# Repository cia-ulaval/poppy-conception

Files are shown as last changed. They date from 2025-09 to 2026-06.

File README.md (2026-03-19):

# Poppy Humanoid (Conception) 🛠️

## Documentation (_How to Poppy_)
- Visiter ce [Google Docs](https://docs.google.com/document/d/1xX1RbV6WdlQWjZE55EWiICiZSR_HosOSyKKz-T2dgOk/edit?usp=sharing).
- Tu trouveras dans ce document les points marquants de la conception du robot, ainsi que de toutes les manoeuvres et manipulations nécessaires à son bon fonctionnement.

## Fiche d'Identité

*   **Type de projet :** Projet Club
*   **Team Lead :** Cyrille Bernier
*   **Partenaire Académique/Industriel :** N/A
*   **Effectif recherché :** 4 membres
*   **Profils recherchés :** Génie mécanique, Impression 3D, Robotique, Électronique

## Description du Projet

Imprimer en 3D et assembler un robot humanoïde Poppy open-source, comprenant l'impression des composants, l'assemblage des 25 articulations motorisées et l'intégration des systèmes électroniques pour créer un robot fonctionnel.

## Objectifs & Livrables

*   **Objectif Principal :** Construire un robot humanoïde Poppy entièrement fonctionnel pour la session d'automne.
*   **Livrables attendus :**
    *   Pièces imprimées en 3D et post-traitées
    *   Structure mécanique assemblée avec 25 articulations
    *   Système électronique intégré et câblé
    *   Documentation complète du processus d'assemblage
    *   Robot fonctionnel prêt pour la programmation

## Timeline Prévisionnelle de la Session

| Semaine | Activité/Phase |
| :-----: | :--- |
|  **1-2**  | **Planification** - Étude des plans |
|  **3-6**  | **Impression 3D** - Production intensive des composants mécaniques |
|  **7-8**  | **Post-traitement** - Finition et préparation des pièces imprimées |
|  **9-12** | **Assemblage mécanique** - Montage des articulations et structure |
|  **13-15**| **Intégration électronique** - Câblage moteurs et capteurs |

## Technologies & Compétences Visées

*   **Logiciels :** Logiciels CAO (SolidWorks/Fusion360), Slicers impression 3D
*   **Matériels :** Imprimantes 3D, moteurs Dynamixel, composants électroniques
*   **Compétences :** Impression 3D, assemblage mécanique, lecture plans techniques, soudure, câblage

## Pourquoi rejoindre ce projet ?

Tu vas aimer ce projet si :
*   Tu aimes travailler de tes mains et voir un projet concret prendre forme
*   Tu es passionné par la robotique et la mécanique
*   Tu veux apprendre les techniques d'impression 3D et d'assemblage robotique professionnel

## Contact & Liens Utiles
*   **Documentation :** [Poppy Project Documentation](https://docs.poppy-project.org/en/assembly-guides/poppy-humanoid/)
*   **Référence :** [GitHub Poppy](https://github.com/poppy-project)
*   **Fichiers imprimables des Body Parts de Poppy:** [Fichiers imprimables](https://github.com/poppy-project/poppy-humanoid/releases/download/hardware_1.0.1/STL_3D_printed_parts.zip)
*   **Excel des pièces:** [Excel](https://ulavaldti-my.sharepoint.com/:x:/r/personal/cyber18_ulaval_ca/Documents/Poppy%20pi%C3%A8ces.xlsx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)
*   **Playlist vidéos d'assemblage:** [Playlist](https://www.youtube.com/watch?v=SUlM_mE3plc&list=PL8wg9_Kkof8wwqgfFu0iCij73C-4gt95x&index=2)
*   **[Body parts en format .sldprt](https://github.com/poppy-project/Poppy-multiarticulated-torso/tree/dffc1e8f4aaba17622789be21f6563d275080ec6/parts)**

- **[Documentation des moteurs qui n'avaient pas d'allure](https://ulavaldti-my.sharepoint.com/:x:/g/personal/cyber18_ulaval_ca/IQDmeS0tiUcpSrYruJAAcc10AX4TU4iCfaX-LsLGC0McrcA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)**
- [Documentation Poppy Eve](https://github.com/poppy-project/Poppy-eva-head-design#poppy-eve-head-design)

# Démarrage du projet

---

## Prérequis

- Dockers : <https://docs.docker.com/desktop/#next-steps>

---

## Démarrage rapide

```bash
docker compose up -d
```

une fois démaré le conteneur est relié en temps réel au dossier src du projet.

---

## Commandes utiles

```bash
# Démarrer
docker compose up -d

# Arrêter
docker compose down

# Attacher au conteneur
sudo docker attach poppy-dev

#détacher du conteneur (ne pas executer dans ton terminal)
exit

# Voir les logs
docker compose logs -f

# Reconstruire après modification de Package.json ou Dockerfile
docker compose up -d --build

# pour avoir de l'aide à propos des commandes dockers
docker --help
docker compose --help

```

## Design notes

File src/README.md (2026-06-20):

# How to Run Project

```txt
IPv4 adress de Poppy : 10.242.180.129
Procédure pour les noobs : 
ssh poppy@10.242.180.129
password : poppyulaval
cd work/poppy-conception
docker compose up -d
docker attach poppy-dev
exit (pour quitter le terminal)
DISPLAY=:0 python3 src/ui/screen.py depuis work/poppy-conception

```

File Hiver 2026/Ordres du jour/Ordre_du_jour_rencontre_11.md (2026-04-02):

## À faire

- Finir l'*exposure* des données des moteurs.
- Connaître les limites de chaque moteur pour normaliser les sorties et dé-normaliser les entrées
- Finir l'Assemblage du nouveau Chest.
- Ajouter les batteries.
- Tester le nouveau circuit (sans tuer Poppy)
- Cable management (apporter des zip ties)
- Prise Jack DC ?

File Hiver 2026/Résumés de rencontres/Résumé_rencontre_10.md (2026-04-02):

# Fait

Specs Batteries et al.
Rencontre avec Jonathan (Simulation Poppy)

## Cad
- Vis : chambrage circulaire pour accueillir la tête de la vis.
- Imprimé le sac a dos.

## Brand	DROK
- Colour	Aluminium Shell
- Item weight	0.11 Kilograms
- Input voltage	24 Volts
- Output voltage	12 Volts

Dimensions : 
- 5.7x3.8x2.2 cm
- 109 g

## Batterie 3Ah 12V
- Dimensions: 4.33 in. x 1.10 in. x 2.95 in. (110 mm x 27 mm x 75 mm)
- Weight: 0.8 lbs. (0.4 kg)

## Software
- API set-uppé.
- Images de Poppy affichées dans le terminal par Tkinter. (Laurik)
- Bonhomme sourire de Poppy.

# À faire
- Imprimer le nouveau chest
- set-upper le full screen sur l'écran de Poppy. 
- Pendaison de Poppy.
- Être capable de GET la position et vélocité des moteurs. Être capable de lancer une commande sur chacun des moteurs.

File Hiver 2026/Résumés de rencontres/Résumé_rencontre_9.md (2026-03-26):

# API
## Fait
- Exploration
- Set-uppé le SSH.
- AUTRE dont je ne me souviens plus.

Batteries : 
- 8 x 3.8 x 4.5 cm
- Fils sortent par en arriere
- PLaque fixée à l'air libre, sur l'extérieur, protégée et isolée par 7 mm de plastique. 
- On ajoutera une couche d'isolant thermique pour le régulateur.
- Vérifier si l'air est un meilleur isolant thermique que le PLA.
    - Air : 0.024 W/mK
- Vérifier la température maximale ambiante pour les batteries.
- Vérifier le wattage thermique (puissance thermique) du régulateur
- Vérifier l'Aire du régulateur : 

### À acheter : 
- Isolant
- Régulateur
- 

Contraintes (cahier des charges) : 
- La distance entre le support transversal et l'intérieur de l'arrière dos du sac a dos > 4.5 cm.
- La distance entre la base de la poignée et le côté intérieur latéral du sac a dos > 3.8 cm.
- Il doit y avoir de l'espace pour faire passer tous les fils derrière la poignée.
- Il doit y avoir un moyen de fixer le SAD (sac a dos) sur le frame de Poppy.
- Il doit y avoir un moyen de fixer le régulateur sur le SAD.
- Il ne faut pas que la chaleur du régulateur fasse fondre le plastique
- Il faut que les batteries soient logées de façon à ne pas bouger pendant les mouvements.

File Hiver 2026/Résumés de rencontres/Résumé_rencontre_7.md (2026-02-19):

- Vérification de max 5 volts pour le condensateur du RPi.
- La prise mâle qui doit entrer dans le SMPS est une prise de type "Jack DC male"
- Il faudra ajouter un module après la batterie. Pour s'assurer que la tension ne descende pas trop.
- [Convertisseur USB-c à Jack DC 5.5mm a 2.1 mm](https://www.amazon.ca/Female-Input-Charge-Laptop-Notebook/dp/B0BPB8BPRP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) Utile si on a une batterie dont l'extrant aboutit sur un USB-c mâle.
- [USB à Jack DC 5.5 mm x 2.1 mm](https://www.amazon.ca/AAOTOKK-Converter-5-5%C3%972-1mm-Connector-Charging/dp/B0B1WY584Y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) 
    - Utile si on a une batterie dont l'extrant aboutit sur un USB mâle. (not so likely...)
- Batterie qui fournit entre 8 et 12 Ah (8000 mmAh, 12000 mmAh) (valeur d'énergie).
- Batterie va shooter 12V fixes. Mais la batterie peut shooter la quantité de Watts qu'on lui demande, dans les plages de valeurs fixées par notre utilisation.
- Li-on ou Lipo-pack-3s ou Life-Po4-4s
    - Li-on : [bon spécimen de 306g](https://www.amazon.ca/Rechargeable-Powerful-Portable-Suitable-Equipment/dp/B0C2Q6DXRL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)
        - Problème : les dimensions et le poids affichés dans l'image sont pour du 6000 mAh... malheureusement.
    - LiPo-pack-3s
- Il nous faut un BMS. Le BMS est le module de protection dont on parlait.
- On pourrait (il serait même souhaitable) brancher deux (2) batteries en série. De cette façon, on pourra sélectionner des batteries ayant moins d'énergie stockée, et donc un volume moindre. Nous placerions deux batteries, une sur chaque flanc de Poppy.

- [Meilleur spécimen qu'on a](https://ca.lightmalls.com/12v-4000mah-18650-lithium-ion-dc-12-6v-super-rechargeable-battery-pack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). 
    - Specs : 4000 mAh, 12V, 7x5x2 cm. Calcul : 38.4 minutes à elle seule à 60W. Donc pour deux batteries comme ça, ça fait 76.8 minutes !

| Type Batterie | Avantage | Désavantages |
| --- | --- | --- |
| Li-on | Le module BMS est intégré. | Charge simple.  |
| Li-Po | Plus efficace, plus compacte, plus puissante | Risques dans le chargement. Peut exploser. Pas de BMS. |

# À faire : 
- Contacter l'Université pour demander si on peut avoir des batteries [comme ceci](https://www.amazon.ca/Rechargeable-Powerful-Portable-Suitable-Equipment/dp/B0C2Q6DXRL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) dans le local PLT-3778.

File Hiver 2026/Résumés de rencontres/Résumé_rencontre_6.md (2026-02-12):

# Fait
- Gérer le *cable management*
- Gainer les fils d'alimentation au RPi
- Utiliser le kit de soudure efficacement.
- Placer les adhérents sur les pieds.
- Fixer la caméra.
- Fixer le dessus de la tête avec les aimants.
- On a brainstorm pour les batteries.
- Note : les pieds adhérents sont un peu un risque au démarrage. Positif pour la marche, douteux pour le *stand_position*

# À faire : 
- Zach : visiter le GAUL pour mieux comprendre les batteries, voir les options.

# Batteries
- On s'est renseignés
- On a besoin de ...
    - 12 V
    - 5 A
    - 60 W
- On essaye que ce soit pas moins au niveau des Watts.
- On essaye que ce soit pas moins ni plus au niveau des Volts.
- Combien de kilowattheures avons-nous besoin ?
- Objectif : on veut 15 mintues
- Contrainte : peut-on recharger les batteries toutes du même coup avec le même fil?
    - Zach : peut-être, si on a un bloc pour toutes les charger d'un coup.
- [Possibilité de batterie. Lien.](https://www.alibaba.com/product-detail/10000mah-Type-C-PD-60W-Power_60637098016.html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)

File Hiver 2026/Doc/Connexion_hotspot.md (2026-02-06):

# Comment lancer des primitives à Poppy à partir de la connexion au Hotspot (pour Windows):

- Installer [Postman](https://www.postman.com/). Le télécharger sur sa propre machine (laptop)
- Ne pas se connecter à Postman avec un compte. Si nécessaire, se connecter puis se déconnecter.
- Lancer le robot (alimentation *on*)
- Se connecter à partir de sa machine sur le hotspot de poppy.
    - Mot de passe : poppyproject
- Aller sur un *browser* web. Rentrer l'ip suivant : 
    - 10.99.99.1
- Cliquer sur le bouton *what is happening ?*
- Reboot Robot API
- Revenir au menu principal
- Aller dans Monitor and Control
- On peut alors voir la température en *live* des moteurs.
- Aller sur Postman sans être connecté.
- Toutes les requêtes commencent par l'ip de poppy et son port : 
    - 10.99.99.1:8080/.......suite
- Lancer la requête GET suivante pour obtenir la liste des primitives: 
    - primitives/list.json
- Liste de toutes les requêtes : 

```txt
/robot.json
/ip.json
/motors/list.json
/motors/aliases/list.json
/motors/<alias>/list.json
/motors/<motor_name>/registers/list.json
/motors/<motor_name>/registers/<register_name>/value.json
/motors/registers/<register_name>/list.json
/sensors/list.json<br>/sensors/<sensor_name>/registers/list.json
/sensors/<sensor_name>/registers/<register_name>/value.json
/sensors/camera/frame.png
/sensors/code/<code_name>.json
/records/list.json
/records/<move_name>/value.json
/primitives/list.json
/primitives/running/list.json
/primitives/<primitive_name>/start.json
/primitives/<primitive_name>/stop.json
/primitives/<primitive_name>/pause.json
/primitives/<primitive_name>/resume.json
/primitives/<primitive_name>/properties/list.json
/primitives/<primitive_name>/properties/<prop>/value.json
/primitives/<primitive_name>/methods/list.json
/ik/<chain_name>/value.json
/ik/<chain_name>/rpy.json

Post method url:
/motors/<motor_name>/registers/<register_name>/value.json
/motors/<motor_name>/goto.json
/motors/goto.json
/sensors/<sensor_name>/registers/<register_name>/value.json
/records/<move_name>/record.json
/records/<move_name>/save.json
/records/<move_name>/play.json
/records/<move_name>/stop.json
/records/<move_name>/delete.json
/primitives/<primitive_name>/properties/<prop>/value.json
/primitives/<primitive_name>/methods/<method_name>/args.json
/ik/<chain_name>/goto.json
```

- Par la suite, on peut lancer des requêtes GET pour les primitives de Poppy, dont notamment stand_position, avec la syntaxe suviante : 
    - 10.99.99.1:8080/primitives/stand_position/start.json
- ATTENTION ! Les primitives qui ne sont pas stoppées avec stop.json reviendront éventuellement dans le comportement de Poppy. Autrement dit, elles ne sont pas arrêtées.

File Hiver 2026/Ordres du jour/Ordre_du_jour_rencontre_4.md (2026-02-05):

# à Faire

- Féliciter Toute l'Équipe, mais spécialement Samy.
- Régler les jambes : 
    - Par herborist (reconfiguration des moteurs) ?
    - Par la mécanique ? (Par l'assemblage)
- Souder

- Configure motors correctly

- Peut-être installer les aimants sur la tête.
- Tester d'Autres positions de base.
- Régler la tête qui se positionne mal dans la position standing.
- Commencer les recherches sur les batteries.
- Brainstorm sur l'installation des logos et batteries.
    - Vérifier les amplitudes de mouvement pour toutes les positions de base. De cette façon, nous pourrons mieux cerner les *spots* de Poppy qui sont disponibles pour l'installation d'une extension.

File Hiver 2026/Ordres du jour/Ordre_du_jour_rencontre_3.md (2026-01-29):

# Salut
# À apporter 
- Plus de tie-wraps.

# À faire
- Vectoriser le logo de l'AESGUL.
- Designer la pièce pour le logo de l'AESGUL (SolidWorks).
- Fixer la tête (dernière étape)
- Coller la caméra (parmi les dernières étapes).
- Aller au magasin d'électronique pour : 
    - Souder les fils noirs et rouges ensemble : noir et noir, rouge et rouge.
    - Ça sert à connecter le RPi au Power venant des RS485 extérieurs.
- *Cable management* : 
    - Fixer les câbles avec des boucles 3D-printed.
    - Ou encore des tie-wraps.
    - Ou encore avec de la colle chaude.
    - Ou encore avec de la gommette.

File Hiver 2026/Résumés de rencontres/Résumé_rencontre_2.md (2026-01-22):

# Fait

- Installation de Herborist sur la machine de Samy.
- Fixation de l'écran sur la tête.
- Connexion du POWER entre les deux SMP2S avec des câbles à 3 brins plutôt que des câbles à 4 brins (Samy).
- Vérification que tous les moteurs sont branchés et présents (scan sur Herborist).
    - Configuration du moteur r_ankle_y.
- 
- Le code est installé (Laurik).
- Installation de la caméra (Zach). Branchée provisoirement.
- Élaboration d'un plan d'action pour la connexion de l'adaptateur RPi. (fils rouge et noir).
- 

# À faire
- Fixer la tête (dernière étape)
- Coller la caméra (parmi les dernières étapes).
- Aller au magasin d'électronique pour : 
    - Souder les fils noirs et rouges ensemble : noir et noir, rouge et rouge.
    - Ça sert à connecter le RPi au Power venant des RS485 extérieurs.
- *Cable management* : 
    - Fixer les câbles avec des boucles 3D-printed.
    - Ou encore des tie-wraps.
    - Ou encore avec de la colle chaude.
    - Ou encore avec de la gommette.

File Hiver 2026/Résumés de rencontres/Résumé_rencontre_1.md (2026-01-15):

# À prévoir
- Imprimer des pièces de rechange pour les pièces qui demanderont des réparations.
- Apporter des tie-wraps / zip-ties pour fixer les *dispatchers* de courant. Minces.

# Fait ajd
- Un peu de documentation
- Préparation fichier STL pour le RPi support (*Head Assembly*)
- Cad pièce alternative pour le *HeadLock* Poppy Eva.
- Derrière de la tête 
- Vérification du cablage dans le torse (samy)
- Documentation session passée (Cyrille)
- Tête Arduino (Zach)
- Batteries recherche (Zach (et Cyrille))
    - Besoin de batterie : 3A, 5V.

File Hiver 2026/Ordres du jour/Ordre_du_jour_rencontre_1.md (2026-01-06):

# Retour sur la session d'automne 2025
## Accomplissements
- Robot assemblé
- Cocktail des projets
- Travail d'équipe et ponctualité
- Plaisir

## À changer. 
- Travailler davantage au VCH-3870 lors des journées de développement (Cyrille doit gérer ça mieux).

## À terminer
- Documentation
- Tête : 
- Raspberry Pi : 
    - Trouver le code en ligne : Samy
    - Partager le lien sur le Discord.
    - Intégrer le code sur le Raspberry Pi : toute l'équipe.
    - **Faire marcher le robot pour la première fois.** Deadline : **30 janvier 2026**

# Plan pour la session d'hiver 2026
## À terminer
Voir ci-haut.
## À entreprendre
- Construction du sac à dos de support de batterie.
    - Conversations avec l'équipe de projets pour savoir si on peut avoir le budget pour se payer cette batterie (Cyrille).
    - Identification des besoins électriques de Poppy (Zach et Laurik et Louis)
    - Consultation sur le web de batteries suffisamment fortes pour soutenir Poppy (Samy et Cyrille)
    - Achat de la batterie si le modèle est compatible (taille, prix, autres contraintes, etc.)
    - Modélisation du sac à dos
        - Décider de la pièce sur laquelle attacher le sac à dos.
        - Décider de la méthode de fixation du sac à dos sur le corps de Poppy.
        - Prévoir un moyen de retirer la batterie pour la recharger, ou encore de la recharger directement lorsque fixée sur Poppy.

## Horaire
- CrabFit.

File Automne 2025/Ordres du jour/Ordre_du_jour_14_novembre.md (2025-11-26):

### À faire : 
- Composer le PowerPoint.
- Demander qui sera présent ?
- ~~Demander qui fera le micro-pitch ?~~
- Qu'est-ce que vous aimeriez montrer de notre démarche dans la présentation, dans le pitch, dans le kiosque.
- Définir le plan de présentation : 
    - Points forts, défis, checkpoints, techniques et méthdoes.
    - 5 minutes de présentation.
- Affiche ?

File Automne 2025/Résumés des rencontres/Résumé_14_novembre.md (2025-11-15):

### Présences : 
- Samy
- Cyrille
- Zach
- Laurik
- 

### *Micro-pitch*:
- Zach se propose de le faire.

### Ce que vous aimeriez avoir de présent dans la présentation de 5 mintues : 
- Défis
- Bons coups
- *Checkpoints*
- Méthodes : 
    - Configuration des moteurs
    - Assemblage avec clés allen
    - Sens des pièces (HN07-N101)
    -

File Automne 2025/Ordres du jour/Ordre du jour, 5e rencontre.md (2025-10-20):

- Remplir le CrabFit pour la formation sur SW
- Commencer à assembler.

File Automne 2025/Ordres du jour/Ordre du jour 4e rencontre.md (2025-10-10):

- Merci Zach pour les impressions !
- Finaliser l'installation des logiciels pour la configuration des moteurs.
- Test de configuration des moteurs.
- Assemblage.

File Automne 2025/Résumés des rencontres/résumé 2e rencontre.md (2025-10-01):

# Résumé de la rencontre 26 septembre 2025

## Résumé de la rencontre
- Laurik ferait des recherches sur la calibraiton de l'imprimante en fonction du type de fil, de la marque du fil.
- À faire pour la semaine prochaine : 
    - Visionner les vidéos

## Paramètres à fixer et commandes utiles

### Paramètres
- Sparse and fill / Gyroid (pattern de filling)
- Strength / Wall loops : 4
- Supports / Top Z distance : entre 0.2 et 0.4. En ce moment, laisser à 0.3 max.  Idéal 0.28
- First layer expansion : 3.0
- Qualité / Layer height : 0.18 mm.

- Project filaments / 
    - 3 points / Edit / Textured PEI plate 60 et 60 degrés Celcius
    - Nozzle initial layer : 220 Celcius, other layers : 190 Celcius.
    

- Supports / 
    - threshold angle = 15
    - remove small overhangs = false
    - initial layer expansion = 2
    - top Z distance = 0.28
    - bottom z distance = 0
    - Base pattern = Hollow
    - Top interface layer = 3

### Commandes
- Commande pour visualiser les zones d'opération de la buse par objet : 
    - Aller dans Objects / Plate1 et placer le curseur sur la pièce pour voir son range.

## Outils nécessaires à apporter
- Petits tournevis
- Pinces précises
- Exacto plus coupant
- Papier sablé 80 - 120

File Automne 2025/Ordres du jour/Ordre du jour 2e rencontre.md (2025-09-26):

| # Numéro  | Description | Notes | 
|---|---|---|
| #1  | Clés ? PLT-3905-Z ? | Louis avait quelque chose à dire là-dessus. (insight) |
| #2 | Retour sur la semaine précédente.  |  |
| #3 |  Qualité des faces...  |  |
| #4 |  Calibration de l'imprimante en fonction du type de fil. |  |
| #5  | Paramètres pour ajuster la distance des supports. | Zach ? |
| #6 |  **Warnings** |  |
| #7 |  Début de l'assemblage | Arrimage des Servo-moteurs sur les bras de Poppy. Vis entre les mains et les avant-bras. |
| #8  | |  |
| # | |  |

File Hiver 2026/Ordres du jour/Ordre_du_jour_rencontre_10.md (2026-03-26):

## À faire

- API.
    - Update sur les avancements de l'API.
- Commander l'électronique.
- Cadder le sac à dos.
- Exporter le fichier du sac à dos et celui du torse de façon à pouvoir les imprimer..
- Est-ce que l'API sera prêt pour le 9 avril prochain ?
- 

Hardware
- Pendaison de Poppy.
- Cadder.

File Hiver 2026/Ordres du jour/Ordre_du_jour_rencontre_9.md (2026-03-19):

# À faire

- Set-upper l'API
    - Samy et Laurik, svp dispatcher les tâches si possible.
    - Peut-on commencer les fichiers code de mouvement pour les moteurs ?
        - Code de la puissance et de l'électricité
        - Code du mouvement angulaire des moteurs.

- Sac à dos : première itération. Deuxième itération en cad.
- Feedback sur la première itération : objectif : avoir de quoi sur lequel pointer pour exprimer nos idées.

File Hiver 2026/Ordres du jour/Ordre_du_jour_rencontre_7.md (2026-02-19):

# À faire : 
- Comment ça va ?
- Tempête des sciences : 
    - Mercredi 15 avril, 11h00 - 16h00
    - Présentation de Poppy.
- Être en mesure de push du code à Poppy :
    - Avec fil
    - Sans fil
- Se renseigner sur la façon de faire marcher Poppy : 
    - Code en ligne ?
    - Possible de le télécharger ?
    - Comment le push sur le RPi ?
- Batteries : nouvelles ?
    - Il faut aussi trouver un fil qui transfère le courant depuis la batterie jusqu'à la prise du *dispatcher* de courant
- Composer du code pour le plaisir de voir Poppy dabber (*sidequest* de Cyrille)

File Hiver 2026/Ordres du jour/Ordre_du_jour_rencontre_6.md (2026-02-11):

# À faire

- ALLO !!!

- Ajouter les aimants pour la tête.
- Fermer la tête pour de bon
- Coller la caméra de façon à ce qu'on puisse l'utiliserr
- Remplacer un câble dans la tête (l'allonger) (celui qui est USB)
- *Set-upper* l'écran
- Gérer la *cable management*
- Ajouter l'adhérent aux chaussures.
- Cadder
- Élaoration de primitives
- Ajouter des gaines permanentes

- Brainstorm sur l'autonomisation de Poppy.

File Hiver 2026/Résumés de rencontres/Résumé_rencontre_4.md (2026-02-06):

# Fait

- Travail sur la connexion WiFi de Poppy. Connexion établie entre le HotSpot de Poppy et le laptop de Samy.
- Vérification pour chaque moteur si oui ou non il est à la bonne place.
- Penser au fait qu'il existe 4 erreurs possibles : 
    1. Erreur de nom de moteur : exemple : le actual l_shoulder_y devrait plutôt être r_shoulder_y.
    2. Erreur de fixation entre le moteur et la roulette métallique.
    3. Erreur de fixation entre la roulette métallique et la pièce de plastique.
    4. Erreur dans le positionnement (notamment le sens, l'orientation) de la pièce de plastique par rapport au moteur. 
- Connexion du laptop de Laurik au Poppy Software
- Soudure
- Fixation de la tête vérifiée (démontage et remontage.) On n'était pas sûrs si elle était bien fixée au niveau du *neck*

### Moteurs à reconfigurer (remplacer le nom dans la configuration)
- l_shoulder_y : FAIT
- r_shoulder_y : FAIT
- Pour cela, il fallait démonter le bras, puis le remonter (longues tâches d'environ 2 heures combinées totales)

### Moteurs desquels replacer le membre
- Aucun

# À faire:
- Changer le mot de passe de Poppy.
- Designer le cable management.

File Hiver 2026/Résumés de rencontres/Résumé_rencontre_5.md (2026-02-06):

# Fait

- Ajout de gaines temporaires sur le les soudures d'étain
- Connecté Cyrille et Laurik (leur laptop)
- Confirmation de présence aux portes ouvertes de l'Université Laval le 7 février. (Samy au moins) Voir doc sur la procédure à suivre pour la connexion au Hotspot de Poppy et le lancement de primitives.

# À faire
- Ajouter les aimants pour la tête.
- Coller la caméra de façon à ce qu'on puisse l'utiliserr
- Remplacer un câble dans la tête (l'allonger) (celui qui est USB)
- *Set-upper* l'écran
- Gérer la *cable management*
- Ajouter l'adhérent aux chaussures.
- Cadder
- Élaoration de primitives
- Ajouter des gaines permanentes

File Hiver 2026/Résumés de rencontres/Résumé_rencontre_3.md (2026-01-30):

# Fait

- Gestion du câblage dans la tête.
- Tentatives d'établissement de la connexion entre le RPi et le WiFi.
- But de ces tentatives : commander Poppy à distance. Exemple : "avance le bras"
- Esquisses de vectorisation du logo de l'AESGUL.
- Démarches de *brainstorming* pour l'installation du logo sur Poppy.

# À faire : 
- Souder les fils pour l'alimentation du Rpi
- Achever la connexion réseau de Poppy (Samy et Laurik)
- Mieux déterminer la nature et l'emplacement des batteries sur Poppy (Zach et Cyrille)
- Poursuivre le travail sur le logo de l'AESGUL.
- Modéliser en 3D le support pour le logo (sûrement par essais-erreurs, ou bien en se fiant au modèle .sldprt suivant : [fichier .sldprt](https://github.com/poppy-project/Poppy-multiarticulated-torso/tree/dffc1e8f4aaba17622789be21f6563d275080ec6/parts))
- Modéliser les supports pour les batteries.
- Peut-être : modéliser une pièce qui aurait pour double fonction de soutenir une batterie et d'afficher le logo du partenaire.

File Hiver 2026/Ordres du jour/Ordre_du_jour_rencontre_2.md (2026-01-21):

# À faire
- Mercredi après-midi : cadder mieux les fixations pour la tête (Cyrille).
- Fixer l'écran à la tête (tous).
- Intégrer le code.
- Fermer la tête.
- Documentation en parallèle.
- Définir les batteries à acheter.
- Définir les pièces supplémentaires à acheter.
- Définir un budget pour toutes ces pièces.

# À apporter
- Patafix (Cyrille)
- Tie-Wraps (Cyrille)

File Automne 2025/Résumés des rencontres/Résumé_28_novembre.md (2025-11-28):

# Débriefing du le cocktail des projets (27 novembre)
- À refaire
- Top de recevoir des idées et des commentaires positifs ewt constrcutiis sur notre projet.
- Les gens étaient vraiment intéresés et curieux sur notre projet.
- Les gens ont beaucoup demandé ce que pourrait éventuellement faire Poppy.
- Les juges nous ont défavorisé parce qu'il n'y avait pas d'IA d'implémentée dans notre projet.
- Voir des gens hors du Club était valorisé pour les Team Members.
- **Plus qu'il y a de monde, mieux c'est.**
- **Les Team Members sont très intéressés par la présence accrue de partenaires et d'autres compagnies non partenaires.**
- 

# Brainstorm pour la suite des choses, (Hiver 2026)
- Poppy comme la nouvelle mascotte du Club.
- Idées : 
    - Samy : sac à dos à batterie.
    - Mains articulées.
    - Tout ce qui a trait à l'automatisation.
    - Renforcer la structure en impression 3D
    - Améliorer l'esthétique de la mascotte du Club. Cacher les lieux de fils et de vis nombreux.
- Zach, Samy et Laurik seraient très heureux de poursuivre le projet à la session d'hiver 2026.

# Liste des choses à faire sur Poppy
- (Conception du sac à dos ?)
- Trouver les specs des moteurs
- Mise au point des problèmes avec la tête.
- Intégration logicielle sur Poppy. Ordre des manipulations.
- Adhésion des pieds.
- Impression de pièces de rechange (?, prévision)
- CAD des adhésions pour les pieds.
- Zach va créer un fichier qui documentera les paramètres des impressions pour chacune des pièces.
- Il faut créer un document *How to Poppy*. Ce sera une tâche commune.
    - Mentionner le GitHub et la playlist des assemblages.
    - Configuration des moteurs.

## Pour réussir à faire marcher Poppy
- Tête à imprimer
- Le câblage à connecter
- L'écran / microprocesseur
- Intégrer le code sur le RP pi.
- Tests avec *power supply* et code en ligne.

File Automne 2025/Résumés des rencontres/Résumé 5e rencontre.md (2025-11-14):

- Écrire un guide d'utilisation pour l'imprimante
- Faire une liste de toutes les pièces de Poppy

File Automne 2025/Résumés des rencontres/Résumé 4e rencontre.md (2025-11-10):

# Avancement ?
- **Bras gauche terminé !!!**
- Samy et Cyrille ont installé poppy-configure sur leur Linux.
- Les moteurs MX-64AT sont montés et configurés.
- Les moteurs des hanches sont montés et configurés.
- Les moteurs des épaules et des bras sont tous configurés.

# Procédure installation poppy-configure
- Être sur Linux.
- Installer un environnement python dans un dossier local.
- Activer cet environnement python avec une commande de type "source bin/activate" (dans poppy-env)
- Installer poppy-configure : python3 install poppy-humanoid
- Commande pour configurer : poppy-configure humanoid < motorname >

# Notes : 
- Acheter et apporter du papier sablé (éventuellement)
- Samy ou Cyrille apporte des clés Allen de tailles plus grosses.

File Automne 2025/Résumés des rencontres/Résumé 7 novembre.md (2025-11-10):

### À apporter pour la prochaine rencontre :
- Pince supplémentaire
- Colle chaude

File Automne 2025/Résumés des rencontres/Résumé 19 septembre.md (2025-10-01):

# Résumé rencontre 19 septembre
- Nous nous sommes présentés.
- Nous avons convenu d'un mode de fonctionnement : se relayer pour imprimer les pièces de *Poppy*.
- Nous avons convenu qu'il pourrait être bénéfique de se synchroniser à 2 étudiants pour les impressions de la première semaine.
- Nous avons convenu du jour et de l'heure des rencontres : **les vendredis 16h30, au PLT-3778**
- Nous avons convenu qu'il fallait que chacun ait accès à la clé du local. 
    - Pour ce faire, vous pouvez aller au local **PLT-3905-G** et demander d'avoir une copie de la clé. Ça requiert un dépôt de 20$, qui vous sera rendu à la fin du projet. Le plus tôt que vous avez la clé, le plus tôt que vous pouvez imprimer de votre côté ! Si vous n'avez pas la clé encore, juste faire signe à Amen Ouannes dans le *group chat* (ou la demander à un autre *Team member*)
- Nous avons discuté des procédures d'impression.

# Procédure d'impression:
1. Importer la pièce dans Bambu Studio.
2. Vérifier la couleur de la pièce.
3. Orienter correctement la pièce pour l'impression. Critères : surface plane par-dessus un vide limitée; les cercles doivent avoir leur rayon dans le plan *xy*.
4. Ajouter les supports si nécessaire.
5. Trancher le plateau.
6. Exporter le fichier tranché sur la clé USB (connetée à la carte SD).
7. Éjecter la clé USB.
8. Insérer la carte micro-SD dans l'imprimante.
9. Choisir le fichier à imprimer.
10. Sélectionner la couleur d'impression.
11. Appuyer sur *Imprimer*.

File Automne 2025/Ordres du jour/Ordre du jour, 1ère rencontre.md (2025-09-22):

| # Numéro  | Description | Notes | 
|---|---|---|
| #1  |  **Présentations**, baccalauréats, intérêts personnels, hobby, phobie, folie.  |  |
| #2 | Présentation de l'**échéancier** pour la session.| Mentionner que c'est modifiable. |
| #3 | Présenter l'**imprimante 3D**. | Julie présentation, demande si les gens connaissent bien l'imprimante 3D. Présenter les paramètres importants. |
| #4 | Présenter la visée des quelques **prochaines semaines**  | Impression intensive, distribution des impressions. Beaucoup du travail se fera individuellement. Logistique des **clés** et des **cartes SD.** |
| #5  | Installation du logiciel **BambuStudio** | Installation du logiciel, importation des membres Poppy Humanoid |
| #6 | **Assigner** les différentes impressions à chacun des membres. | |
| #7 | Impression collective de la **première pièce** de *Poppy*. | |
| #8  | Convenir d'une **plage horaire** dans la semaine où nous pouvons nous rencontrer pendant la session. Utilisation de CrabFit. | |
| # | | |

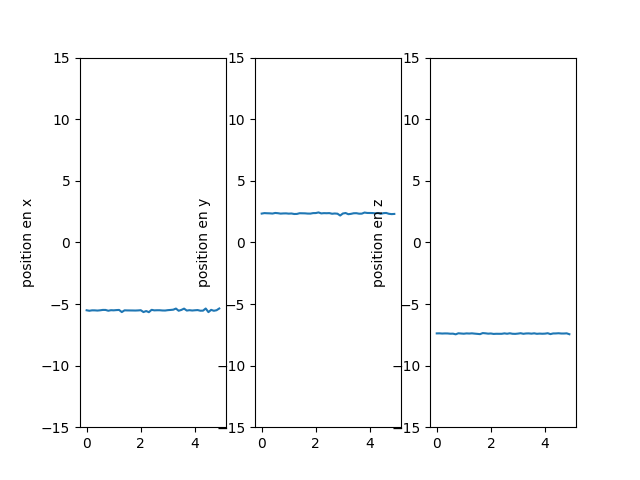
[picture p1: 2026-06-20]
src/accelerometres/avec_le_clone/acceleration.png

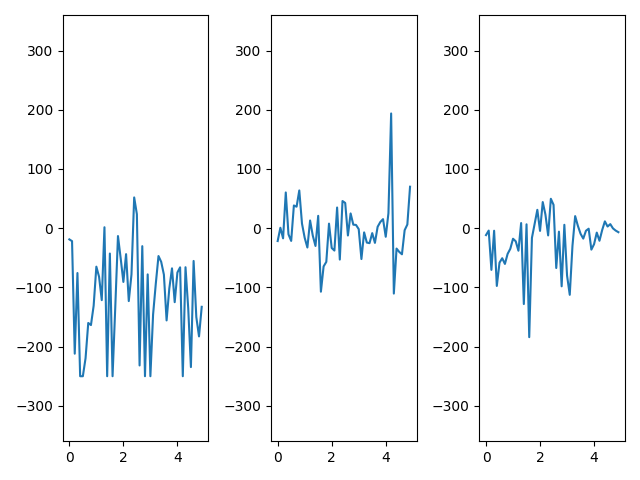
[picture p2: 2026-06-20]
src/accelerometres/avec_le_clone/angles.png

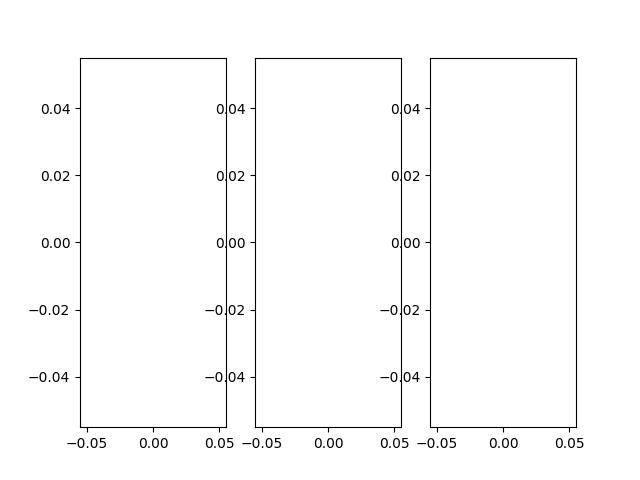
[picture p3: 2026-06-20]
src/accelerometres/avec_le_clone/vitesses_angulaires_live.png

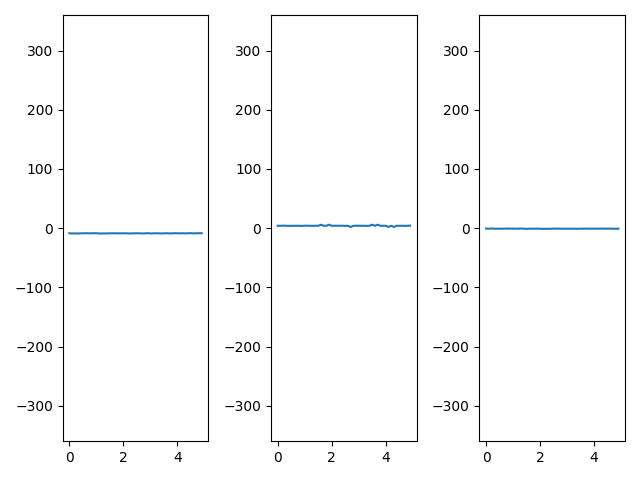
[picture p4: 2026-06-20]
src/accelerometres/avec_le_clone/vitesses_angulaires.png

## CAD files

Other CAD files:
connexion m28 manquante.gcode.3mf

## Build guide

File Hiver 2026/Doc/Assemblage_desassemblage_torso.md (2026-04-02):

Enlever bras
Enlever shoulder connecter
Enelver les moteurs cen traux

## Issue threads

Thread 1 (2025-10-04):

Preprocess the data.

JeromeCGithub, 2025-10-04:
On a pris un set de donnée avec le bracelet qui se trouve sur la branche :

Ce ticket consiste à analyser la donnée, la comprendre puis splitter la data avec scikit en training data et en target data. Voir la doc de scikit : https://scikit-learn.org/stable/modules/generated/sklearn.discriminant_analysis.LinearDiscriminantAnalysis.html

Ensuite, essayer d'entrainer des modèles avec plusieurs algorithmes trouvable ici : https://libemg.github.io/libemg/documentation/prediction/prediction.html

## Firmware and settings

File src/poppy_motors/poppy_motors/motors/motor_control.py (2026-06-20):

from time import perf_counter, time

from dynamixel_sdk import (COMM_SUCCESS, PortHandler,PacketHandler, GroupSyncWrite, GroupBulkRead)
from concurrent.futures import ThreadPoolExecutor


PORTS = ['/dev/ttyACM0','/dev/ttyACM1']
PROTOCOL = 1.0
ID_RANGE = range(0, 55)
BAUDRATE = 1000000





class MotorController:
    """
    Manages communication with multiple motors over serial ports, handling
    port initialization, baud rate configuration, motor ID mapping, and
    resource cleanup.
    """


   


    def __init__(self):
        self.port_handlers : list[PortHandler] = [PortHandler(port) for port in PORTS]
        self.packet_handler : PacketHandler = PacketHandler(PROTOCOL)
        self.id_port_map : dict[int, PortHandler] = {}
        self.write_methods: dict[int, callable] = {
            1: self.packet_handler.write1ByteTxRx,
            2: self.packet_handler.write2ByteTxRx,
            4: self.packet_handler.write4ByteTxRx,
        }
        self.read_methods: dict[int, callable] = {
            1: self.packet_handler.read1ByteTxRx,
            2: self.packet_handler.read2ByteTxRx,
            4: self.packet_handler.read4ByteTxRx,
        }

        

        print("Opening Port Handlers...")
        for port_handler in self.port_handlers:
            if not port_handler.openPort():
                raise IOError(f"Cannot open port {port_handler.getPortName()}")

        print("Setting Baud Rates...")
        for port_handler in self.port_handlers:
            if not port_handler.setBaudRate(BAUDRATE):
                raise IOError(f"Failed to set baud rate for port {port_handler.getPortName()}")
        
        print("Scanning for motors and creating ID to port mapping...")
        self._create_id_port_map()
        print("MotorController initialized successfully")
            
    def write(self, motor_id: int, address: int,value: int, byte_size: int) -> None:
        """
        Writes data to a motor with the specified ID at the given address.
        Raises KeyError if the motor ID is not found in id_port_map.
        """
        if motor_id not in self.id_port_map:
            raise ValueError(f"Motor ID {motor_id} not found on any port")
        
        if not byte_size in self.write_methods:
            raise ValueError(f"Unsupported byte size {byte_size} for write operation")
        
        
        port_handler = self.id_port_map[motor_id]
        write_method = self.write_methods[byte_size]
        result, error = write_method(port_handler, motor_id, address, value)

        if result != COMM_SUCCESS:
            raise IOError(f"Failed to write to motor ID {motor_id} at address {address}: {self.packet_handler.getTxRxResult(result)}")
        elif error != 0:
            raise IOError(f"Error from motor ID {motor_id} at address {address}: {self.packet_handler.getRxPacketError(error)}")

    def read(self, motor_id: int, address: int, byte_size: int) -> int:
        """
        Reads data from a motor with the specified ID at the given address.
        Returns the read value as an integer. Raises KeyError if the motor ID
        is not found in id_port_map.
        """
        if motor_id not in self.id_port_map:
            raise ValueError(f"Motor ID {motor_id} not found on any port")
        
        if not byte_size in self.read_methods:
            raise ValueError(f"Unsupported byte size {byte_size} for read operation")
        
        port_handler = self.id_port_map[motor_id]
        read_method = self.read_methods[byte_size]
        value, result, error = read_method(port_handler, motor_id, address)

        if result != COMM_SUCCESS:
            raise IOError(f"Failed to read from motor ID {motor_id} at address {address}: {self.packet_handler.getTxRxResult(result)}")
        elif error != 0:
            raise IOError(f"Error from motor ID {motor_id} at address {address}: {self.packet_handler.getRxPacketError(error)}")
        
        return value  
    
    def sync_write(self, address: int, values_by_id: dict[int, int], byte_size: int) -> None:
        """
        Protocol 1.0 Sync Write:
        Write the same register address/size for multiple motors in one packet per port.
        """
        if not values_by_id:
            return
        if byte_size not in (1, 2, 4):
            raise ValueError(f"Unsupported byte size {byte_size} for sync_write")

        ids_by_port = self._group_ids_by_port(list(values_by_id.keys()))

        for port_handler, motor_ids in ids_by_port.items():
            if not motor_ids:
                continue

            group = GroupSyncWrite(port_handler, self.packet_handler, address, byte_size)

            for motor_id in motor_ids:
                param_bytes = self._value_to_little_endian_bytes(values_by_id[motor_id], byte_size)
                if not group.addParam(motor_id, param_bytes):
                    group.clearParam()
                    raise IOError(f"Failed to add sync_write param for motor ID {motor_id}")

            result = group.txPacket()
            group.clearParam()

            if result != COMM_SUCCESS:
                raise IOError(
                    f"Sync write failed on port {port_handler.getPortName()} at address {address}: "
                    f"{self.packet_handler.getTxRxResult(result)}"
                )
            
    def bulk_read(self, requests_by_id: dict[int, tuple[int, int]]) -> dict[int, int]:
        """
        Protocol 1.0 Bulk Read:
        reading from multiple addresses at the same time
        """
        if not requests_by_id:
            return {}

        results: dict[int, int] = {}
        ids_by_port = self._group_ids_by_port(list(requests_by_id.keys()))

        for port_handler, motor_ids in ids_by_port.items():
            if not motor_ids:
                continue

            group = GroupBulkRead(port_handler, self.packet_handler)

            for motor_id in motor_ids:
                address, byte_size = requests_by_id[motor_id]
                if byte_size not in (1, 2, 4):
                    raise ValueError(f"Unsupported byte size {byte_size} for motor ID {motor_id}")

                if not group.addParam(motor_id, address, byte_size):
                    group.clearParam()
                    raise IOError(f"Failed to add bulk read param for motor ID {motor_id}")

            result = group.txRxPacket()
            if result != COMM_SUCCESS:
                group.clearParam()
                raise IOError(
                    f"Bulk read failed on port {port_handler.getPortName()}: "
                    f"{self.packet_handler.getTxRxResult(result)}"
                )

            for motor_id in motor_ids:
                address, byte_size = requests_by_id[motor_id]
                if not group.isAvailable(motor_id, address, byte_size):
                    group.clearParam()
                    raise IOError(f"Data not available for motor ID {motor_id} at address {address}")

                results[motor_id] = group.getData(motor_id, address, byte_size)

            group.clearParam()

        return results
    
    def _create_id_port_map(self):
        """
        Scans all port_handlers and maps detected motor IDs in ID_RANGE to their
        corresponding ports in id_port_map by pinging each motor.
        """
        with ThreadPoolExecutor(max_workers=len(self.port_handlers)) as executor:
            for port_mappings in executor.map(self._scan_port_for_motors, self.port_handlers):
                self.id_port_map.update(port_mappings)


    def _scan_port_for_motors(self, port_handler: PortHandler) -> dict[int, PortHandler]:
        """
        Scan a single port for all possible motor IDs and return the detected
        mappings for that port.
        """
        port_mappings: dict[int, PortHandler] = {}
        for motor_id in ID_RANGE:
            _, result, _ = self.packet_handler.ping(port_handler, motor_id)
            if result == COMM_SUCCESS:
                port_mappings[motor_id] = port_handler
        return port_mappings
    
    
    
    def _group_ids_by_port(self, motor_ids: list[int]) -> dict[PortHandler, list[int]]:
        grouped: dict[PortHandler, list[int]] = {port_handler: [] for port_handler in self.port_handlers}
        for motor_id in motor_ids:
            if motor_id not in self.id_port_map:
                raise ValueError(f"Motor ID {motor_id} not found on any port")
            grouped[self.id_port_map[motor_id]].append(motor_id)
        return grouped


    def _value_to_little_endian_bytes(self, value: int, byte_size: int) -> list[int]:
        if byte_size not in (1, 2, 4):
            raise ValueError(f"Unsupported byte size {byte_size}")
        # Keep only the requested width, then pack little-endian
        mask = (1 << (byte_size * 8)) - 1
        value &= mask
        return [(value >> (8 * i)) & 0xFF for i in range(byte_size)]
    
    def get_motors(self) -> list[int]:
        """
        Returns a list of all motor IDs that are currently mapped to ports.
        """
        return list(self.id_port_map.keys())


    def close(self):
        """
        Closes all port handlers managed by the MotorController.
        """
        for port_handler in self.port_handlers:
            port_handler.closePort()
    
    
#if __name__ == "__main__":
#    start = perf_counter()
#    controller = MotorController()
#    elapsed = perf_counter() - start
#    print(f"_create_id_port_map took {elapsed:.3f}s")
#    print("Detected motors:", controller.get_motors())
#    controller.sync_write(address=30, values_by_id={54: 3000,44:512}, byte_size=2) 
#    print(controller.bulk_read(requests_by_id={54: (36, 2), 44: (36, 2)}))
#    controller.close() 
        

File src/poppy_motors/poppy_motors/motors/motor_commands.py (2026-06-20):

from .control_table import ControlTable
from .motor_control import MotorController

class MotorCommands:
    """
    A class to encapsulate motor command operations, providing a clean interface for reading and writing to motor registers.
    """

    def __init__(self):
        self.motor_control = MotorController()

    # getters for configuration (EEPROM) operations

    def get_motor_ids(self) -> list[int]:
        """
        Returns a list of motor IDs that are currently mapped to ports.
        """
        return self.motor_control.get_motors()

    def get_model_number(self, motor_id: int) -> int:
        """
        Reads the model number of the motor with the given ID.
        """
        return self.motor_control.read(motor_id, ControlTable.EEPROM.MODEL_NUMBER.value, byte_size=2)

    def get_max_torque(self, motor_id: int) -> int:
        """
        Reads the maximum torque of the motor with the given ID.
        """
        return self.motor_control.read(motor_id, ControlTable.EEPROM.MAX_TORQUE.value, byte_size=2)

    def get_cw_angle_limit(self, motor_id: int) -> int:
        """
        Reads the maximum CW angle limit of the motor with the given ID.
        """
        return self.motor_control.read(motor_id, ControlTable.EEPROM.CW_ANGLE_LIMIT.value, byte_size=2)
    
    def get_ccw_angle_limit(self, motor_id: int) -> int:
        """
        Reads the maximum CCW angle limit of the motor with the given ID.
        """
        return self.motor_control.read(motor_id, ControlTable.EEPROM.CCW_ANGLE_LIMIT.value, byte_size=2)


    # Getters for RAM operations (read operations) 
    
    def get_goal_position(self, motor_id: int) -> int:
        """
        Reads the goal position of the motor with the given ID.
        """
        return self.motor_control.read(motor_id, ControlTable.RAM.GOAL_POSITION.value, byte_size=2)
    
    def get_torque_limit(self, motor_id: int) -> int:
        """
        Reads the torque limit of the motor with the given ID.
        """
        return self.motor_control.read(motor_id, ControlTable.RAM.TORQUE_LIMIT.value, byte_size=2)
    
    def get_moving_speed(self, motor_id: int) -> int:
        """
        Reads the maximum moving speed of the motor with the given ID.
        """
        return self.motor_control.read(motor_id, ControlTable.RAM.MOVING_SPEED.value, byte_size=2)
    
    def get_all_present_position_MX(self) -> dict[int,int]:
        
        motorsDict : dict ={}
        for motor in self.motor_control.get_motors():
            if self.get_model_number(motor) == (29 or 310): # Mx-64 and Mx-28 model numbers they can use bulk_read
                motorsDict.update({motor:(ControlTable.RAM.PRESENT_POSITION.value, 2)})
            
        return self.motor_control.bulk_read(motorsDict)

    def get_present_position(self, motor_id: int) -> int:
        """
        Reads the present position of the motor with the given ID.
        """
        return self.motor_control.read(motor_id, ControlTable.RAM.PRESENT_POSITION.value, byte_size=2)

    def get_present_moving_speed(self, motor_id: int) -> int:
        """
        Reads the present moving speed of the motor with the given ID.
        """
        return self.motor_control.read(motor_id, ControlTable.RAM.PRESENT_SPEED.value, byte_size=2)

    def get_present_load(self, motor_id: int) -> int:
        """
        Reads the present load of the motor with the given ID.
        """
        return self.motor_control.read(motor_id, ControlTable.RAM.PRESENT_LOAD.value, byte_size=2)


    def get_temperature(self, motor_id: int) -> int:
        """
        Reads the present temperature of the motor with the given ID.
        """
        return self.motor_control.read(motor_id, ControlTable.RAM.PRESENT_TEMPERATURE.value, byte_size=1)

    # Setters for RAM operations

    def torque_enable(self, motor_id: int, enable: bool) -> None:
        """
        Enables or disables torque on the motor with the given ID.
        """
        enable_value = 1 if enable else 0
        self.motor_control.write(motor_id, ControlTable.RAM.TORQUE_ENABLE.value, enable_value, byte_size=1)
    
    def torque_disable_all(self) -> None:
        """
        Disables torque on all motors.
        """
        for motor_id in self.get_motor_ids():
            try:
                self.torque_enable(motor_id, False)
            except IOError as e:
                print(f"Error disabling torque for motor ID {motor_id}: {e}")

    def torque_enable_all(self) -> None:
        """
        Enables torque on all motors.
        """
        for motor_id in self.get_motor_ids():
            try:
                self.torque_enable(motor_id, True)
            except IOError as e:
                print(f"Error enabling torque for motor ID {motor_id}: {e}")

    def set_goal(self, motor_id: int, position: int) -> None:
        """
        Sets the goal position of the motor with the given ID.
        """
        min_angle = self.get_cw_angle_limit(motor_id)
        max_angle = self.get_ccw_angle_limit(motor_id)
        if position > min_angle and position < max_angle:
            self.motor_control.write(motor_id, ControlTable.RAM.GOAL_POSITION.value, position, byte_size=2)
    
    def set_goal_percent(self, motor_id: int, percent: float):
        """
        Sets the percent goal position of the motor with the given ID.
        """
        min_angle = self.get_cw_angle_limit(motor_id)
        max_angle = self.get_ccw_angle_limit(motor_id)
        pos =  min_angle + int((max_angle -min_angle)/100 * percent)
        print(motor_id, pos)
        self.set_goal(motor_id,pos)

    def set_all_goal_percent(self,percent):
        for motor_id in self.get_motor_ids():
            self.set_goal_percent(motor_id, percent)

    def set_moving_speed(self, motor_id: int, speed: int) -> None:
        """
        Sets the moving speed of the motor with the given ID.
        """
        self.motor_control.write(motor_id, ControlTable.RAM.MOVING_SPEED.value, speed, byte_size=2)
    
    def set_torque_limit(self, motor_id: int, torque_limit: int) -> None:
        """
        Sets the torque limit of the motor with the given ID.
        """
        self.motor_control.write(motor_id, ControlTable.RAM.TORQUE_LIMIT.value, torque_limit, byte_size=2)


    def set_all_moving_speed(self, speed: int) -> None:
        """
        Sets the moving speed of all motors to the given value.
        """
        for motor_id in self.get_motor_ids():
            self.set_moving_speed(motor_id, speed)

    def set_all_torque_limit(self, torque_limit: int) -> None:
        """
        Sets the torque limit of all motors to the given value.
        """
        for motor_id in self.get_motor_ids():
            self.set_torque_limit(motor_id, torque_limit)
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

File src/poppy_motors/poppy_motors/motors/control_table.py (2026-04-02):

"""
Dynamixel Protocol 1.0 — Control Table Addresses
=================================================
Structure
---------
  EEPROM          — addresses shared across AX, MX-28/64, and MX-106
  RAM             — addresses shared across AX, MX-28/64, and MX-106
                    (addresses 26–29 are excluded: they differ per family)

  AXRAMDiff       — AX-only RAM registers (compliance, addresses 26–29)
  MXEEPROMDiff    — MX-28/64-only EEPROM registers (multi-turn, resolution)
  MXRAMDiff       — MX-28/64-only RAM registers (PID gains 26–29, realtime
                    tick, goal acceleration)
  MX106EEPROMDiff — MX-106-only EEPROM registers (same extras as MX + higher
                    voltage limit default — documented in class docstring)
  MX106RAMDiff    — MX-106-only RAM registers (PID, realtime tick, current,
                    torque control mode, goal torque, goal acceleration)

Sources (ROBOTIS e-Manual):
    AX-12A : https://emanual.robotis.com/docs/en/dxl/ax/ax-12a/
    MX-28  : https://emanual.robotis.com/docs/en/dxl/mx/mx-28/
"""

from enum import IntEnum


# ===========================================================================
# Common EEPROM  —  identical address and meaning on AX, MX-28/64, MX-106
# ===========================================================================

class EEPROMAddress(IntEnum):
    MODEL_NUMBER        = 0   # 2-byte  R    Model number
    FIRMWARE_VERSION    = 2   # 1-byte  R    Firmware version
    ID                  = 3   # 1-byte  RW   Motor ID (0–253; 254 = broadcast)
    BAUD_RATE           = 4   # 1-byte  RW   Baud rate selector (see BaudRate enum)
    RETURN_DELAY_TIME   = 5   # 1-byte  RW   Status packet delay (unit: 2 µs)
    CW_ANGLE_LIMIT      = 6   # 2-byte  RW   CW  angle limit (0–1023 AX / 0–4095 MX)
    CCW_ANGLE_LIMIT     = 8   # 2-byte  RW   CCW angle limit (0–1023 AX / 0–4095 MX)
    TEMPERATURE_LIMIT   = 11  # 1-byte  RW   Max internal temperature (°C)
    MIN_VOLTAGE_LIMIT   = 12  # 1-byte  RW   Min operating voltage (unit: 0.1 V)
    MAX_VOLTAGE_LIMIT   = 13  # 1-byte  RW   Max operating voltage (unit: 0.1 V)
    MAX_TORQUE          = 14  # 2-byte  RW   Max torque (0–1023, unit: ~0.1 %)
    STATUS_RETURN_LEVEL = 16  # 1-byte  RW   When to send status packets
    ALARM_LED           = 17  # 1-byte  RW   Bitmask: LED blinks on these errors
    SHUTDOWN            = 18  # 1-byte  RW   Bitmask: motor shuts down on these errors


# ===========================================================================
# Common RAM  —  identical address and meaning on AX, MX-28/64, MX-106
# ===========================================================================

class RAMAddress(IntEnum):
   
    TORQUE_ENABLE       = 24  # 1-byte  RW   0 = free / 1 = torque on
    LED                 = 25  # 1-byte  RW   0 = off  / 1 = on
    # 26–29 differ per family — see AXRAMDiff / MXRAMDiff / MX106RAMDiff
    GOAL_POSITION       = 30  # 2-byte  RW   Target position
    MOVING_SPEED        = 32  # 2-byte  RW   Target speed (0–1023 joint / 0–2047 wheel)
    TORQUE_LIMIT        = 34  # 2-byte  RW   Runtime torque limit (0–1023)
    PRESENT_POSITION    = 36  # 2-byte  R    Current position
    PRESENT_SPEED       = 38  # 2-byte  R    Current speed
    PRESENT_LOAD        = 40  # 2-byte  R    Current load (bit10 = direction)
    PRESENT_VOLTAGE     = 42  # 1-byte  R    Input voltage (unit: 0.1 V)
    PRESENT_TEMPERATURE = 43  # 1-byte  R    Internal temperature (°C)
    REGISTERED          = 44  # 1-byte  R    1 if REG_WRITE instruction is pending
    MOVING              = 46  # 1-byte  R    1 while motor is moving toward goal
    LOCK                = 47  # 1-byte  RW   1 = EEPROM locked until power cycle
    PUNCH               = 48  # 2-byte  RW   Minimum drive current


# ===========================================================================
# AX-series differences
# ===========================================================================

class AXRAMAddress(IntEnum):
    CW_COMPLIANCE_MARGIN    = 26  # 1-byte  RW   Dead-band CW  (0–255)
    CCW_COMPLIANCE_MARGIN   = 27  # 1-byte  RW   Dead-band CCW (0–255)
    CW_COMPLIANCE_SLOPE     = 28  # 1-byte  RW   Torque slope CW  (7 steps: 2,4,8,16,32,64,128)
    CCW_COMPLIANCE_SLOPE    = 29  # 1-byte  RW   Torque slope CCW (7 steps: 2,4,8,16,32,64,128)


# ===========================================================================
# MX-28 / MX-64 differences
# ===========================================================================

class MXEEPROMAddress(IntEnum):
    MULTI_TURN_OFFSET  = 20  # 2-byte  RW   Position offset applied in multi-turn mode
    RESOLUTION_DIVIDER = 22  # 1-byte  RW   Divides encoder resolution (1–4)


class MXRAMAddress(IntEnum):
    D_GAIN            = 26  # 1-byte  RW   Derivative gain
    I_GAIN            = 27  # 1-byte  RW   Integral gain
    P_GAIN            = 28  # 1-byte  RW   Proportional gain
    REALTIME_TICK     = 50  # 2-byte  R    Time counter (ms); wraps at 32767
    GOAL_ACCELERATION = 73  # 1-byte  RW   Goal acceleration (~8.583 °/s² per unit; 0 = max)





# ===========================================================================
# Helper enums for common register values
# ===========================================================================

class BaudRate(IntEnum):
    """
    Selector values for EEPROM.BAUD_RATE (address 4).
    Formula:  Speed (bps) = 2,000,000 / (Value + 1)
    """
    BPS_1000000 = 1
    BPS_500000  = 3
    BPS_400000  = 4
    BPS_250000  = 7
    BPS_200000  = 9
    BPS_115200  = 16
    BPS_57600   = 34
    BPS_19200   = 103
    BPS_9600    = 207


class StatusReturn(IntEnum):
    """Values for EEPROM.STATUS_RETURN_LEVEL (address 16)."""
    PING_ONLY = 0   # Reply only to PING
    READ_ONLY = 1   # Reply to READ instructions as well
    ALL       = 2   # Reply to every instruction (default)


class AlarmBit(IntEnum):
    """
    Bitmask constants for EEPROM.ALARM_LED (addr 17) and EEPROM.SHUTDOWN (addr 18).
    Combine with bitwise OR:
        AlarmBit.OVERHEATING | AlarmBit.OVERLOAD
    """
    INPUT_VOLTAGE = 0x01
    ANGLE_LIMIT   = 0x02
    OVERHEATING   = 0x04
    RANGE         = 0x08
    CHECKSUM      = 0x10
    OVERLOAD      = 0x20
    INSTRUCTION   = 0x40


class TorqueEnable(IntEnum):
    """Values for RAM.TORQUE_ENABLE (address 24)."""
    OFF = 0
    ON  = 1


class LEDState(IntEnum):
    """Values for RAM.LED (address 25)."""
    OFF = 0
    ON  = 1


class LockState(IntEnum):
    """Values for RAM.LOCK (address 47)."""
    UNLOCKED = 0
    LOCKED   = 1   # Requires power cycle to unlock


class TorqueCtrlMode(IntEnum):
    """Values for MX106RAMDiff.TORQUE_CTRL_MODE (address 70)."""
    DISABLED = 0   # Normal position / speed control
    ENABLED  = 1   # Pure torque control via MX106RAMDiff.GOAL_TORQUE
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

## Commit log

2025-11-10 poppy-résumé-5e-rencontre
    [connexion m28 manquante.gcode.3mf]
2025-11-26 Ajout de la présentation de Poppy pour le site web
2026-01-06 Ajout d'une étape dans la hiérarchie du repo
2026-02-19 résumé rencontre 7 H26
    [Poppy pièces v2.xlsx]
2026-03-26 basic motor control ser up
2026-04-01 added control-table which contains all the register for motor commands. added read and write to motor_control. added some commands to motor_commands
2026-04-02 created functional commands to poppy motors
2026-04-02 changed docker file to copy the whole repo in the container. Added gitingore for certain folders. changed motor commands to remove main
2026-04-08 adding motor_node.py
2026-04-08 deleted redundant motors folder
2026-04-09 feat: motor node can handle simulation at 0.01 seconds of sleep
    [connexion m28 manquante.gcode.3mf]
2026-05-16 -fixed commands from simulation
    [motor_commands.py, motor_node.py, motor_node_test.py]
2026-05-24 added sync_write and bulk_read to motor_control.py.
2026-06-20 acceleromètre
2026-06-20 Update poppy to current state
